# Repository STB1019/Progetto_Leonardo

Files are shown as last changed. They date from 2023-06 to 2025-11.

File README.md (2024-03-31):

<br/>
<p align="center">
  <h1 align="center">Progetto Leonardo</h1>

  <p align="center">
    An IEEE Student Branch Project
    <br/>
    <br/>
  </p>
</p>

<!--![Downloads](https://img.shields.io/github/downloads/STB1019/Progetto_Leonardo/total) ![Contributors](https://img.shields.io/github/contributors/STB1019/Progetto_Leonardo?color=dark-green)  ![Issues](https://img.shields.io/github/issues/STB1019/Progetto_Leonardo) ![Stargazers](https://img.shields.io/github/stars/STB1019/Progetto_Leonardo?style=social)
-->
## Table Of Contents

* [About the Project](#about-the-project)
* [Built With](#built-with)
* [Roadmap](#roadmap)
* [Authors](#authors)

## About The Project

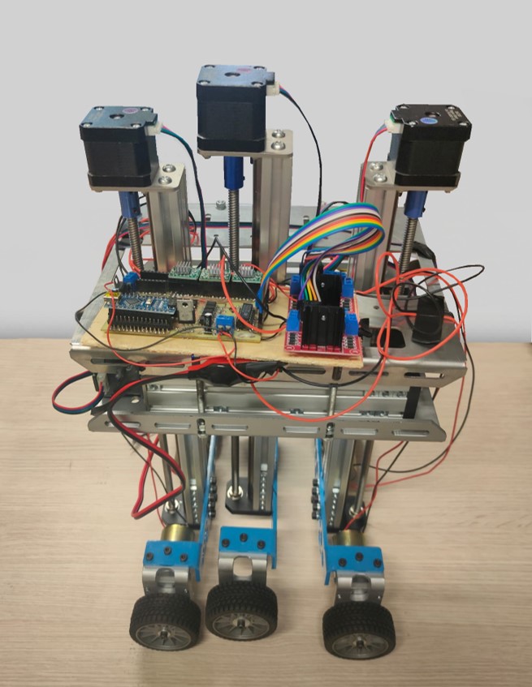
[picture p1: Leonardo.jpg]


Project with the aim of building a robot that is able to move and climb stairs.

## Built With

Raspberry and Arduino

## Roadmap

See the [open issues](https://github.com/TTT357C/Progetto_Leonardo/issues) for a list of proposed features (and known issues). </br>
See also our trello [Trello](https://trello.com/b/dbFiTYEp/progetto-leonardo-ieee-student-branch-brescia)

## Authors

* **Thomas Causetti** - *Engineering Student and Member of IEEE* - [Thomas Causetti](https://github.com/TTT357C/) - *Programmer and Designer*
* **Mirko Rossi** - *Engineering Student and Member of IEEE* - [Mirko Rossi](https://github.com/Zphyr19) - *Programmer*
* **Abdel** - *Engineering Student and Member of IEEE* - [Abdel](https://github.com/99Abdel) - *Programmer*
* **Stefano Molari** - *Engineering Student and Member of IEEE* - [Stefano Molari](https://github.com/steMola) - *Circuit Designer*

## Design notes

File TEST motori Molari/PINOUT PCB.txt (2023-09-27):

STEPPER 1
	7 - DIR
	8 - STEP 

STEPPER 2 
	9 - DIR
	10 - STEP 

STEPPER 3
	11 - DIR
	12 - STEP 

STEPPER 4
	13 - DIR
	AO - STEP 

CONNETTORE LATERALE SINISTRO
 ( DA ALTO VERSO BASSO )

5
!5 
4
!4
3
!3
2
!2

6 PWM

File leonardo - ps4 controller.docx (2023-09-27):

Modulo USB:

https://maker.pro/arduino/projects/how-to-control-an-arduino-robot-with-a-ps4-bluetooth-controller

LoRa:

https://docs.arduino.cc/learn/communication/lorawan-101

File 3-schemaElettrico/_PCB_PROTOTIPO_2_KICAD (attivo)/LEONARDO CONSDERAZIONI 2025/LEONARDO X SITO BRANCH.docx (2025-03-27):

LEONARDO 2.0

COSA È

Leonardo è la prosecuzione di un progetto storico, è essenzialmente un veicolo a batteria in grado di muoversi in ambiente urbano, riuscendo a salire anche le scale.

È stato sviluppato un primo prototipo, il cui miglioramento è stato ostacolato dal poco tempo a disposizione dei vari membri

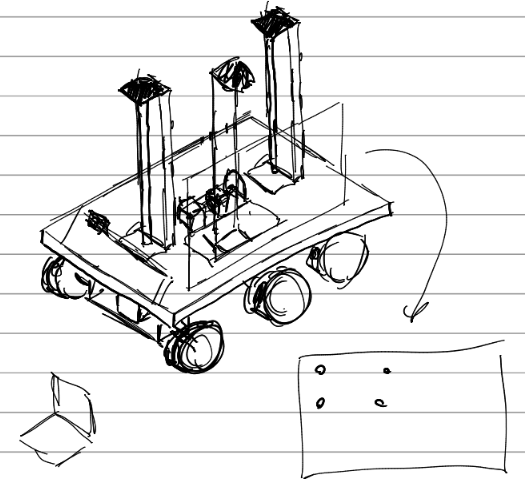
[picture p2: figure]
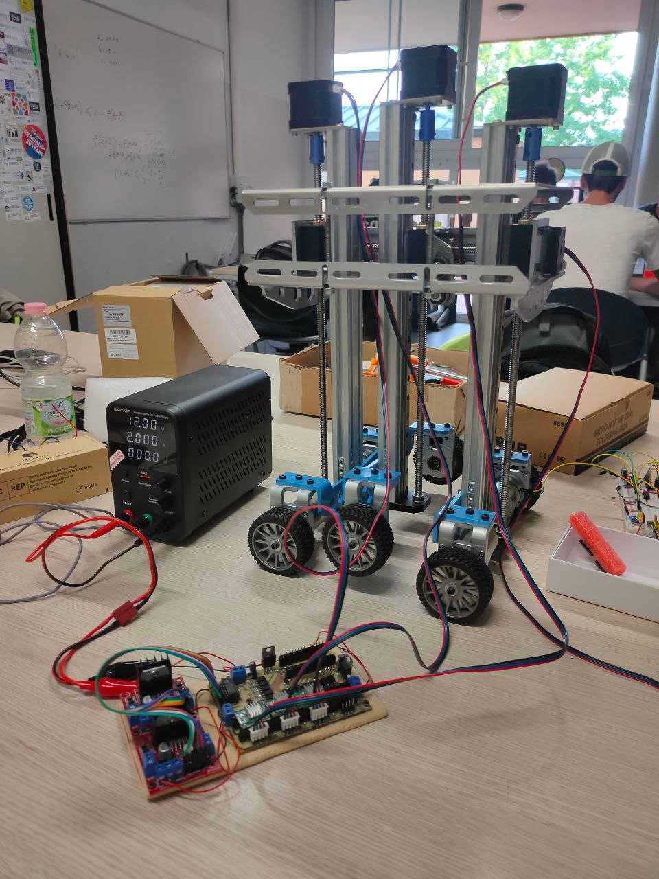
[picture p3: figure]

COSA HA A BORDO

- 4 motori DC muniti di ruota gommata per il movimento orizzontale
- 3 motori stepper che pilotano 3 assi lineari per il movimento vertivale
- 1 motore stepper per spostare l’asse centrale orizzontalmente
- Una scheda elettronica di comando dei motori
- Una rasperry PI

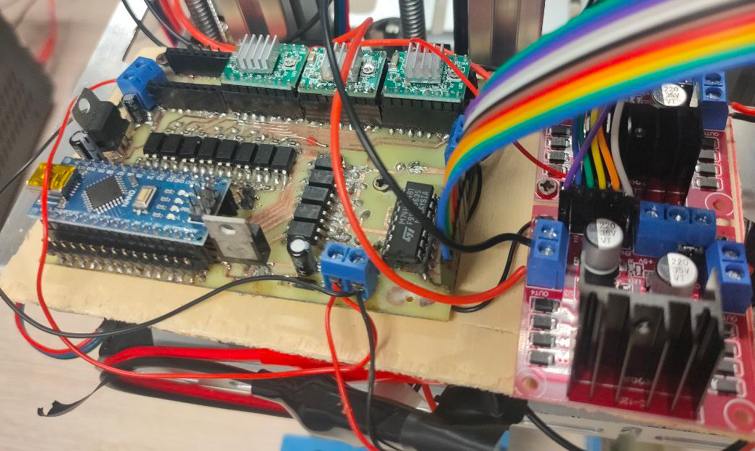
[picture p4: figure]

PROBLEMI ATTUALI

L’elettronica è da rifare, visto che si tratta di una versione base, non ottimizzata, che aveva il solo scopo di dimostrare una effettiva realizzabilità dell’idea. Bisogna migliorare gli aspetti di power saving, visto che è un sistema a batteria. Il firmware e il software sono da integrare con la nuova elettronica.

LAVORI IN CORSO

Si è pensato di adottare un’architettura modulare in modo da poter garantire flessibilità verso sviluppi futuri. È in programma lo sviluppo di:

- Una board per distribuire efficacemente la potenza a tutte le schede del sistema, si ipotizza di tipologia switching per garantire un’efficienza sopra al 90%
- Una board che si interfaccia ai servomotori e ai motori DC, occupandosi quindi di pilotare i movimenti del mezzo
- Una board che si occupa di acquisire posizione ei segnali dall’ambiente circostante, fornendo le informazioni necessarie alla navigazione del mezzo.
- Un raspberry PI che faccia da mente, occupandosi di acquisire i segnali dalla board sensori e di produrre gli output necessari alla board motori

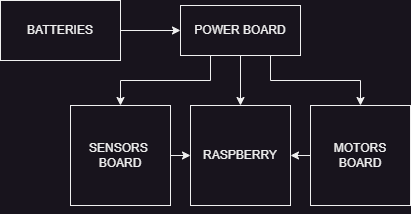
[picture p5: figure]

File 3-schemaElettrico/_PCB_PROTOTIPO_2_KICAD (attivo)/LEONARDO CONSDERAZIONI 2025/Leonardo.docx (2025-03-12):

Partendo dal presupposto che si vuole riciclare la meccanica precedente

STEPPER MOTOR DRIVER

https://lastminuteengineers.com/a4988-stepper-motor-driver-arduino-tutorial/

Dal datasheet a4988

Per maggiore flessibilità è stato lasciata al firmware la scelta del microstep resolution del motore.

I 4 driver saranno collegati tra di loro.

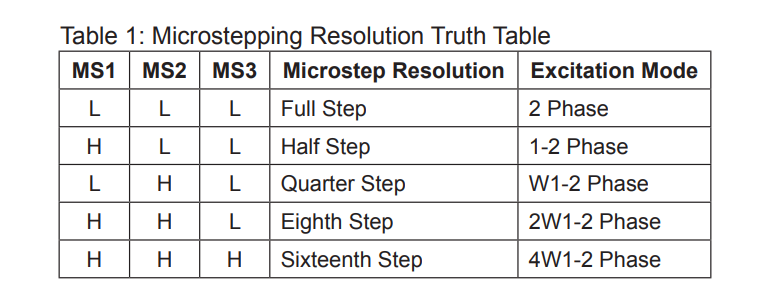
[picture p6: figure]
Immagine che contiene testo, Carattere, schermata, numero Il contenuto generato dall'IA potrebbe non essere corretto.

BATTERY LEVEL

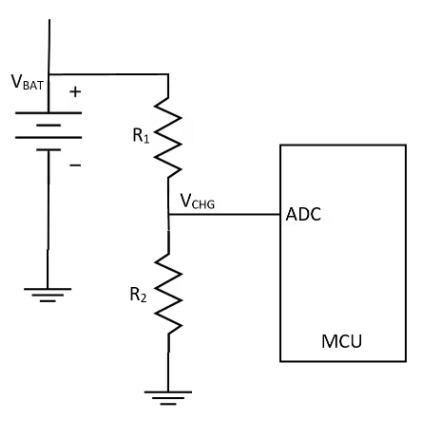
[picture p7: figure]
Immagine che contiene diagramma, schizzo, Disegno tecnico, Piano Il contenuto generato dall'IA potrebbe non essere corretto.

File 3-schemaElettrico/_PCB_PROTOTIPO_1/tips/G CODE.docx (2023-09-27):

G CODE

; Ender 3 Custom Start G-code

G92 E0 ; Reset Extruder

G28 ; Home all axes

G1 Z2.0 F3000 ; Move Z Axis up little to prevent scratching of Heat Bed

G1 X0.1 Y20 Z0.3 F5000.0 ; Move to start position

G1 X0.1 Y200.0 Z0.3 F1500.0 E15 ; Draw the first line

G1 X0.4 Y200.0 Z0.3 F5000.0 ; Move to side a little

G1 X0.4 Y20 Z0.3 F1500.0 E30 ; Draw the second line

G92 E0 ; Reset Extruder

G1 Z2.0 F3000 ; Move Z Axis up little to prevent scratching of Heat Bed

G1 X5 Y20 Z0.3 F5000.0 ; Move over to prevent blob squish

G0 si muove senza estrudere

G1 si muove con l’estrusore

G90 set posizione assoluta

G91 set posizione relativa

G28 auto home

M104

M109

M140

M190

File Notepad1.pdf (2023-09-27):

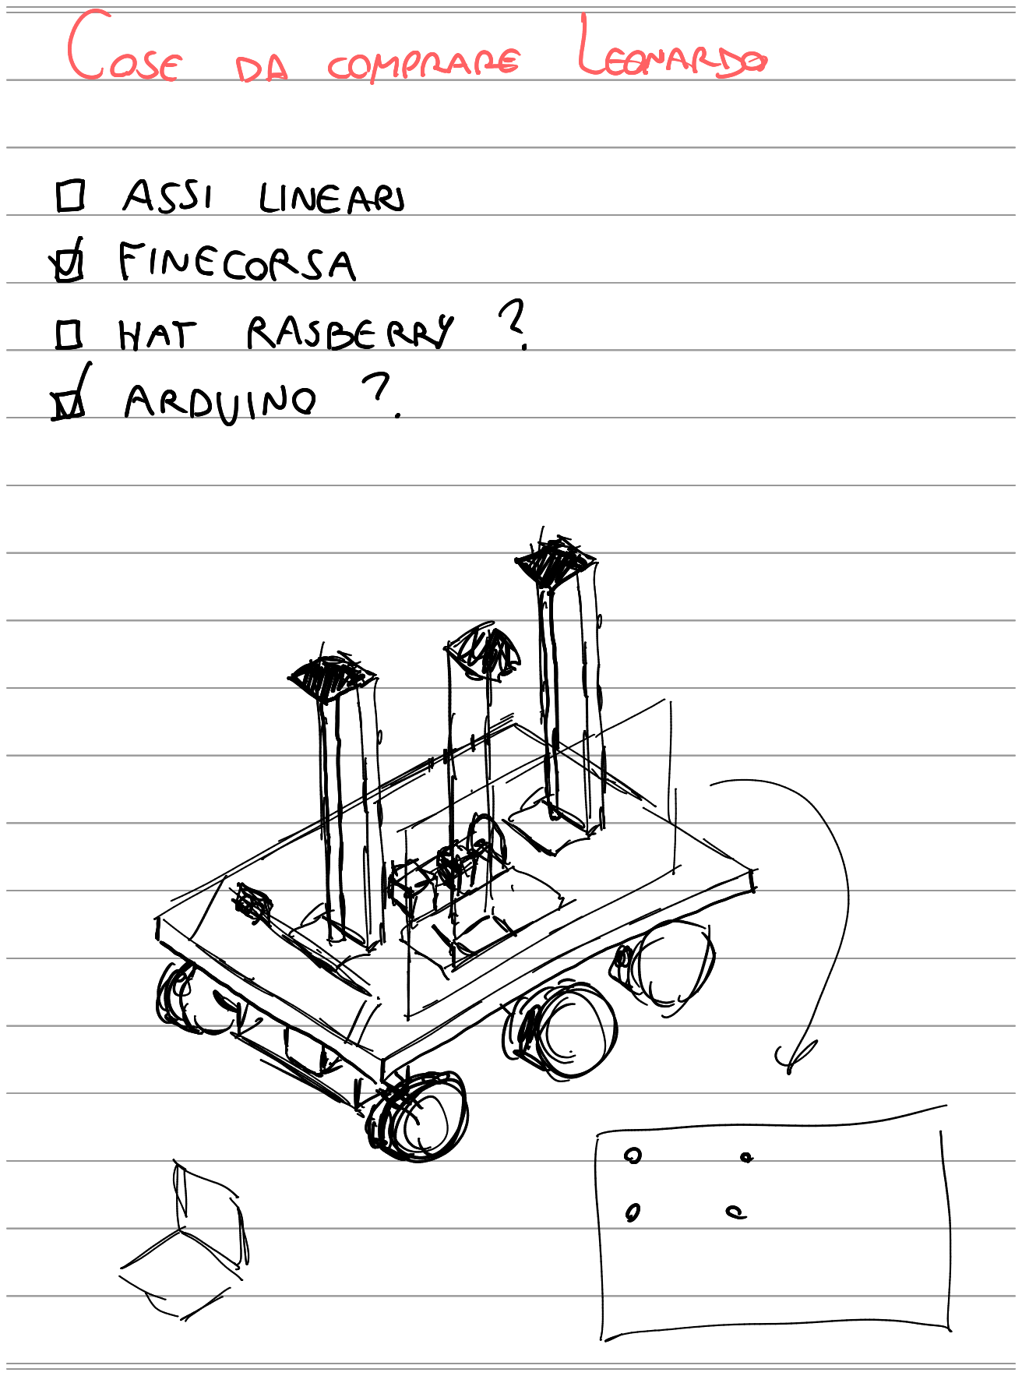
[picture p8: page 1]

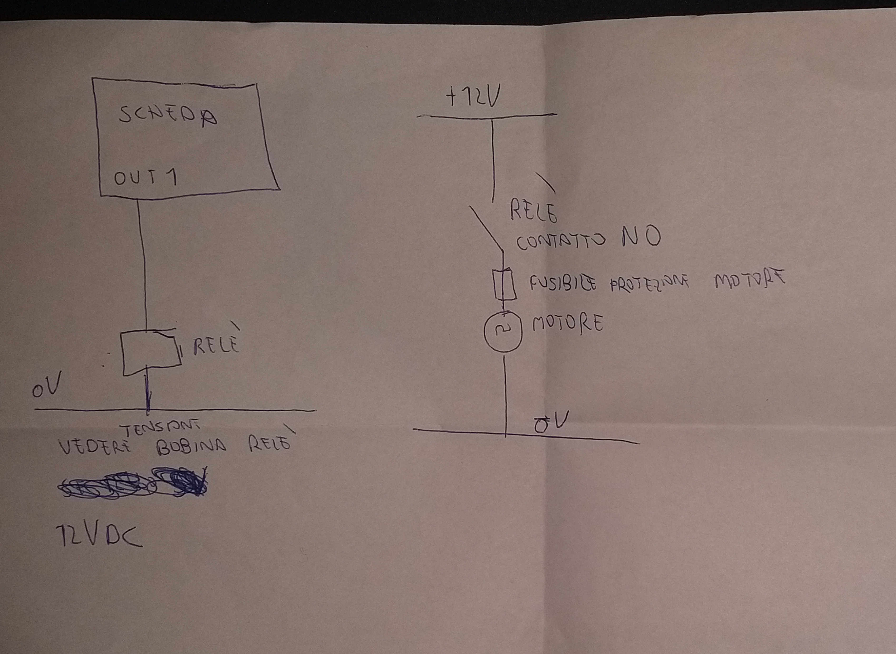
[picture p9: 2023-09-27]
PROTO_SCHEMA_MOTORI.jpg

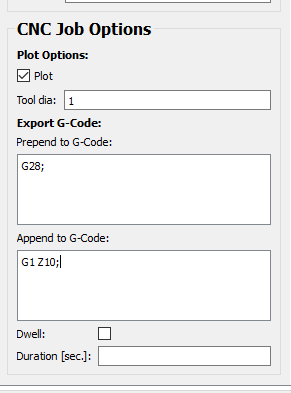
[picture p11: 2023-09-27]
3-schemaElettrico/_PCB_PROTOTIPO_1/02 FLATCAM/CNC OPTIONS.PNG

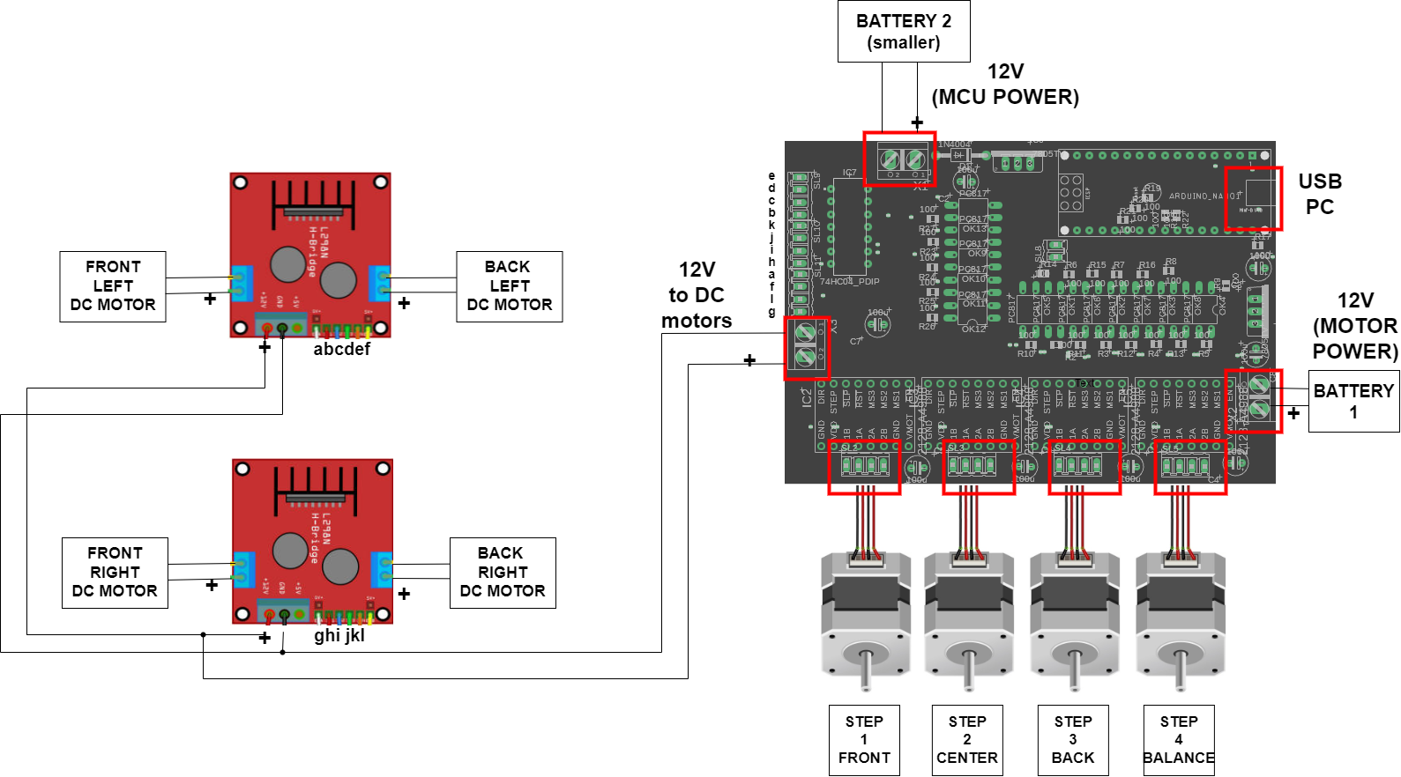
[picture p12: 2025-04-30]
3-schemaElettrico/_PCB_PROTOTIPO_1/PCB Leonardo.drawio.png

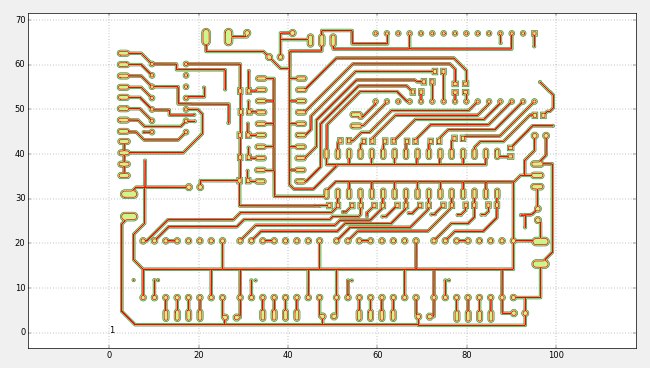
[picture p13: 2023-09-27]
3-schemaElettrico/_PCB_PROTOTIPO_1/02 FLATCAM/foto copper top iso.PNG

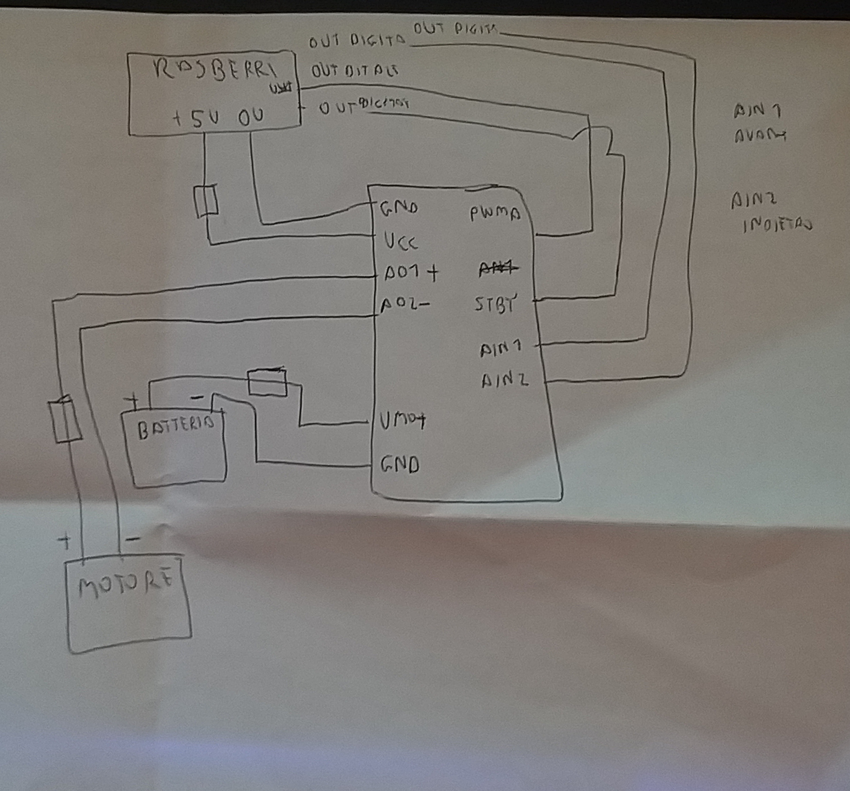
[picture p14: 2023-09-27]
4-Datasheet/vario scartato/MOTORI_LEONARDO_2.jpg

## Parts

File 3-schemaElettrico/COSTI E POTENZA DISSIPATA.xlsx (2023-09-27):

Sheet: COSTO
NOME | COSTO UNITARIO | QUANTITA' | COSTO PARZIALE
ASSE LINEARE
DRIVER A4966 |  | 4
DRIVER TB6612FNG |  | 2
ARDUINO NANO |  | 1
BATTERIE
OPTO ISOLATORI

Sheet: CONSUMI
POTENZA DISPONIBILE |  |  |  | consumo fisso
 |  |  |  | (indipendente dalla fase in cui mi trovo)
POTENZA DISSIPATA TOTALE
 | TEMPO DI FUNZIONAMENTO MASSIMO DEL SISTEMA
 | CONSUMO PER SALIRE LE SCALE
 | componenti attivi | qtà | P singolo
 | stepper | 4
 | dc | 4
 | optoisolatori | 12
 | comsumo fisso
 | CONSUMO PER GIRARE SOLO CON I DC
 | componenti attivi | qtà | P singolo
 | dc | 4
 | optoisolatori | 4
 | comsumo fisso
 | CONSUMO RASPBERRY
 | CONSUMO ARDUINO

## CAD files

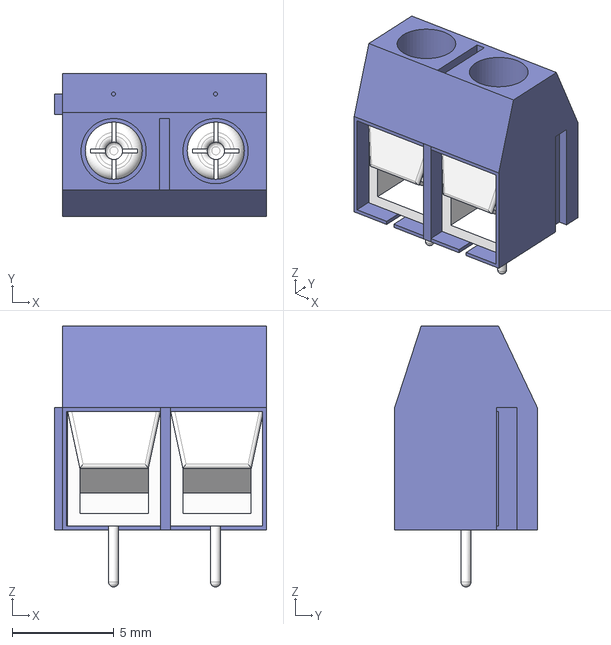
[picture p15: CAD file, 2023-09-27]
3-schemaElettrico/3D MODELS/ak500 - 2.step
10.4 x 7.00 x 12.8 mm

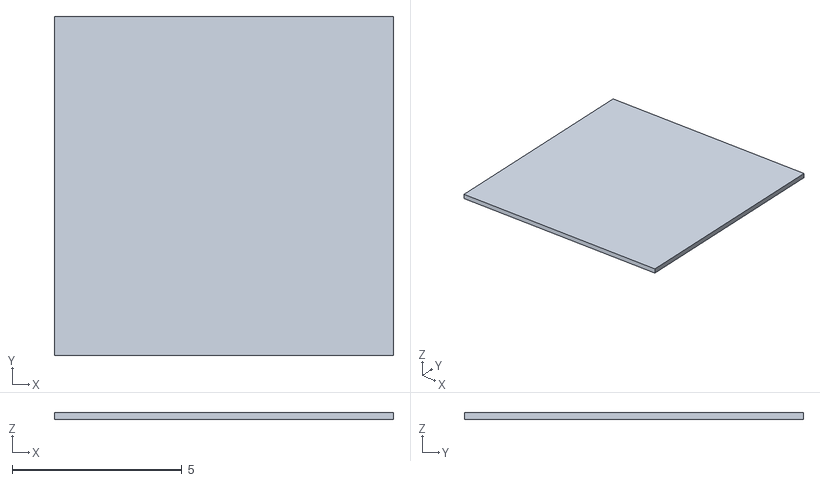
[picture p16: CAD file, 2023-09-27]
3-schemaElettrico/_PCB_PROTOTIPO_1/tips/ORIGINE.stl
10.0 x 10.0 x 0.2

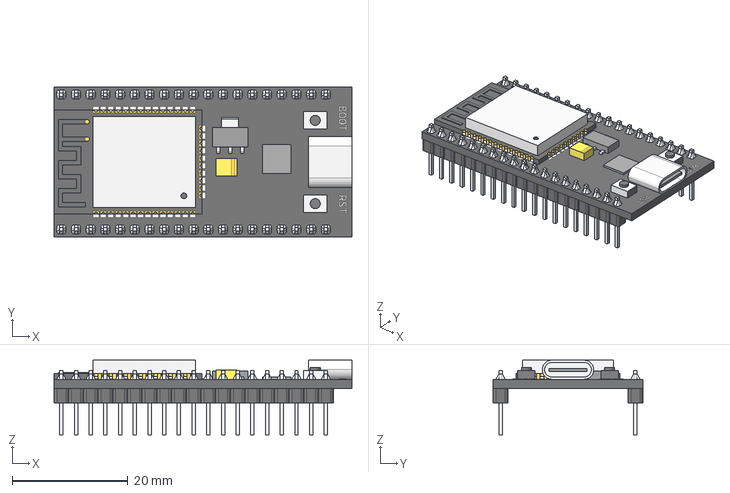
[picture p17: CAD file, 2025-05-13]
3-schemaElettrico/_PCB_PROTOTIPO_2_KICAD (attivo)/LIBRERIE ESTERNE/NodeMCU-32S-USBC-38pin-Narrow.stp
51.5 x 25.9 x 12.9 mm

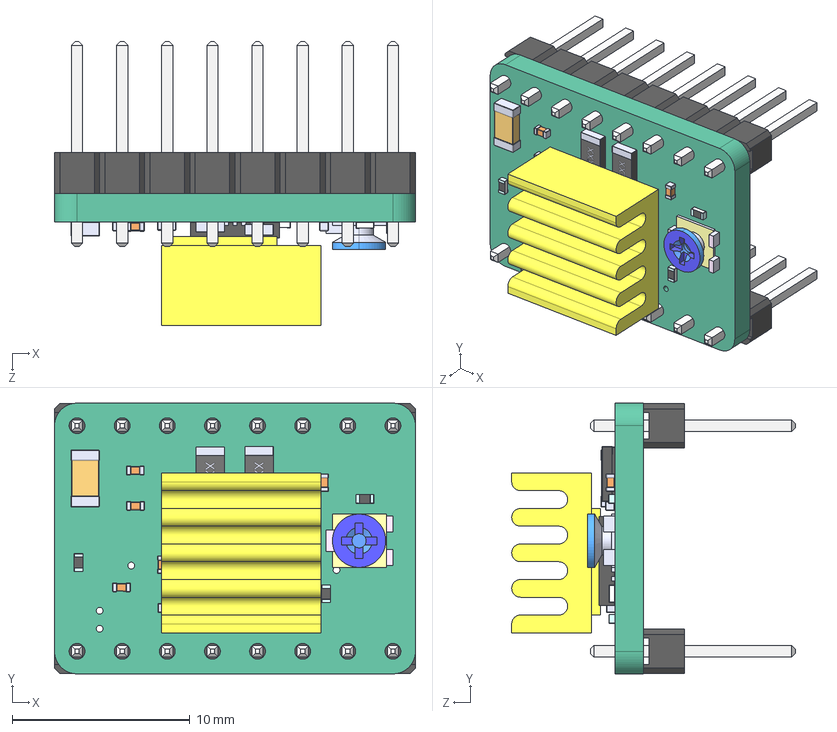
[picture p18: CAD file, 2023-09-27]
3-schemaElettrico/3D MODELS/A4988-1.STEP
20.3 x 15.2 x 16.0 mm
stepstick
QFN28ET_A4983
TRIMPOT3MM_TRIMPOTSMD
Pin header pitch 2.54mm_08 contacts x 2
Heatsink For A4988
R0402-01 x 4
R1206-01 x 2
C0402 x 6
C1206B

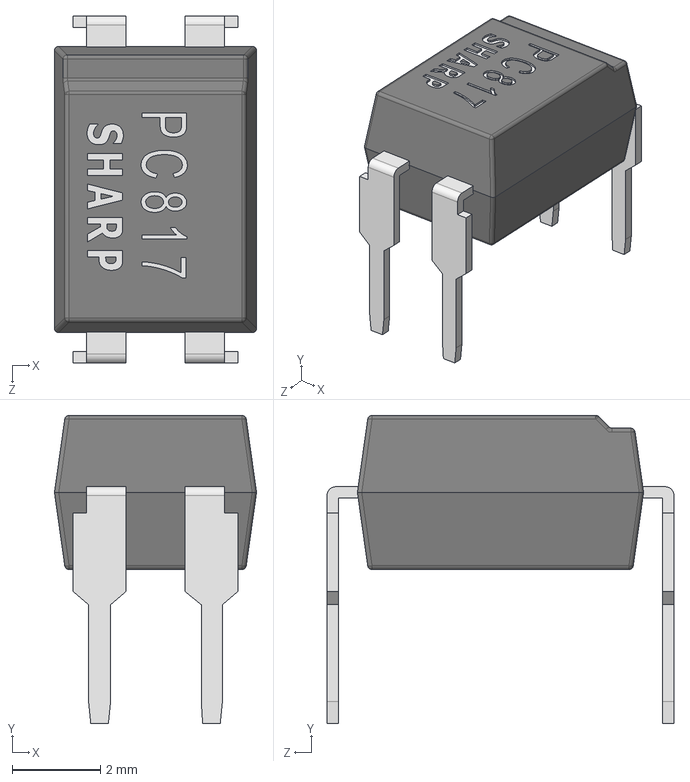
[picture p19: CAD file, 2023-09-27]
3-schemaElettrico/3D MODELS/pc817 dip6.step
4.59 x 7.00 x 7.88 mm

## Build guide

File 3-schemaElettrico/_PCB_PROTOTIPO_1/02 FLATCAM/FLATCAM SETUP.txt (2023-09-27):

open "gerber bottom"
	tool dia -0.6
	offset y70
	offset x69 y82
	generate 
iso
	travel z 4
	generate 
cnc
	tool dia 1
	prepend: G28; per autohome all'inizio
	append: G1 Z10; per alzare la punta alla fine
	generate gerber

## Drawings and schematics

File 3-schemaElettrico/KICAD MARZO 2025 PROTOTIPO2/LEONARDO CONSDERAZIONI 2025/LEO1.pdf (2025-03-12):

REVISION | DESCRIPTION | DATE | APPROVED | REV. SHT. <SCH DWG NO> 1 DWG. NO.

## BATTERY

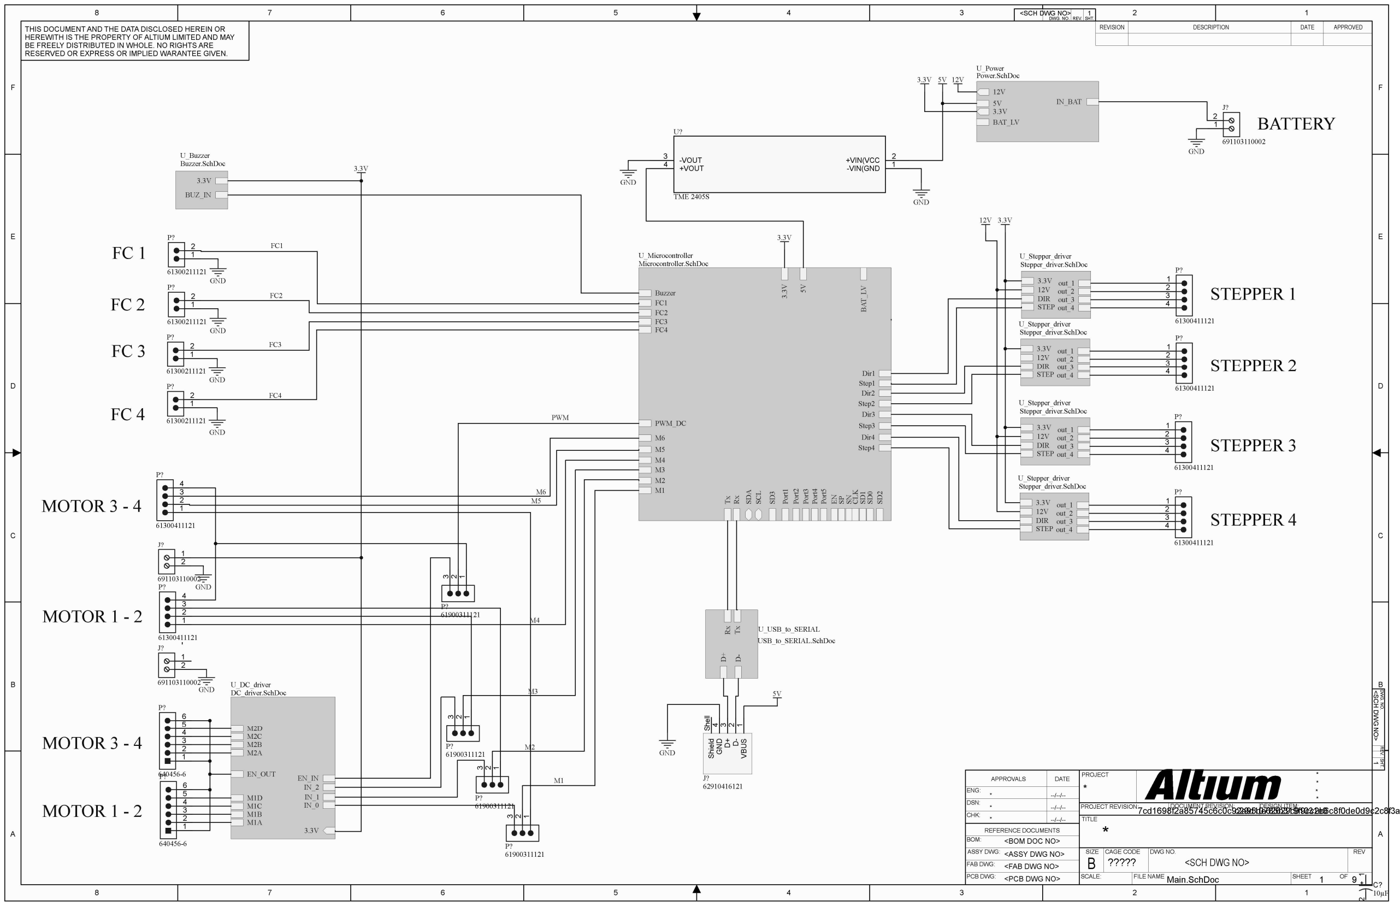
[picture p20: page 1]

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
DWG. NO. REV. SHT.

<SCH DWG NO> 1

THIS DOCUMENT AND THE DATA DISCLOSED HEREIN OR HEREWITH IS THE PROPERTY OF ALTIUM LIMITED AND MAY BE FREELY DISTRIBUTED IN WHOLE. NO RIGHTS ARE RESERVED OR EXPRESS OR IMPLIED WARANTEE GIVEN.

*

B <SCH DWG NO>

Main.SchDoc | 1 | 9

TITLE

SIZE | DWG NO.
FILE NAME | SHEET | OF

REV

SCALE:

?????

CAGE CODE

PROJECT
* | *
| *

*
*
APPROVALS | DATE

ENG:

DSN:

*

*

--/--/--

--/--/--
CHK:
--/--/--
REFERENCE DOCUMENTS
BOM:

ASSY DWG:

FAB DWG:
PCB DWG: <PCB DWG NO>

<FAB DWG NO>

<ASSY DWG NO>

<BOM DOC NO>

*

PROJECT REVISION: | DOCUMENT REVISION: | DESIGN ITEM: 7cd1698f2a85745c6c0c92a95de62629c91031e0 c29d10785b319f9cc2b6c8f0de0d9c2c8f3a0468 1 2

10µF

C?

BUZ_IN

3.3V

U_Buzzer
Buzzer.SchDoc

GND

2
1

P?

61300211121

GND

2
1

P?

61300211121

GND

2
1

P?

61300211121

GND

2
1

P?

61300211121

2

1

3
4

P?

61300411121

STEP

DIR

3.3V
12V

out_1
out_2
out_3
out_4

U_Stepper_driver
Stepper_driver.SchDoc

2

1

3
4

P?

61300411121

STEP

DIR

3.3V
12V

out_1
out_2
out_3
out_4

U_Stepper_driver
Stepper_driver.SchDoc

2

1

3
4

P?

61300411121

STEP

DIR

3.3V
12V

out_1
out_2
out_3
out_4

U_Stepper_driver
Stepper_driver.SchDoc

2

1

3
4

P?

61300411121

STEP

DIR

3.3V
12V

out_1
out_2
out_3
out_4

U_Stepper_driver
Stepper_driver.SchDoc

3.3V

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
IN_0

IN_1

IN_2

EN_IN EN_OUT

U_DC_driver
DC_driver.SchDoc

1

2

3

4

5

6

P?

640456-6

1

2

3

4

5

6

P?

640456-6

## MOTOR 3 - 4

## MOTOR 1 - 2

## STEPPER 1

## STEPPER 2

## STEPPER 3

## STEPPER 4

FC 1

FC 2

FC 3

FC 4

1
2

J?

691103110002

1
2

J?

691103110002

Dir1
Step1
Dir2
Step2
Dir3
Step3
Dir4

Step4 ³.3V TxRx SDA SCL SD³ Port1 Port2 Port3 Port4 Port5 ENSPSNCLK SD¹ SD⁰ SD² ⁵V

M2

M3

M4

M5

M6

Buzzer

FC3

FC1

FC4

FC2

M1

PWM_DC | BAT_LV

U_Microcontroller
Microcontroller.SchDoc

## MOTOR 1 - 2

## MOTOR 3 - 4

3

2

1

P?

61900311121 ³

2

1

P?

61900311121 ³

2

1

P?
61900311121

3

2

1

P?
61900311121 2
1

3

4

P?

61300411121

2
1

3

4

P?

61300411121

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
3.3V

5V

BAT_LV

IN_BAT

U_Power
Power.SchDoc

1

2

J?

691103110002
GND

GND

GND | D⁺ | D⁻ RxTx | U_USB_to_SERIAL
USB_to_SERIAL.SchDoc VBUS

### 1 D- 2 D+

### 3 GND

## 4 Shield Shell

J?
62910416121

GND

3.3V 5V 12V

12V 3.3V

3.3V

5V

-VIN(GND | 1
+VIN(VCC | 2

-VOUT 3
+VOUT 4

U?

TME 2405S

GND

GND

3.3V

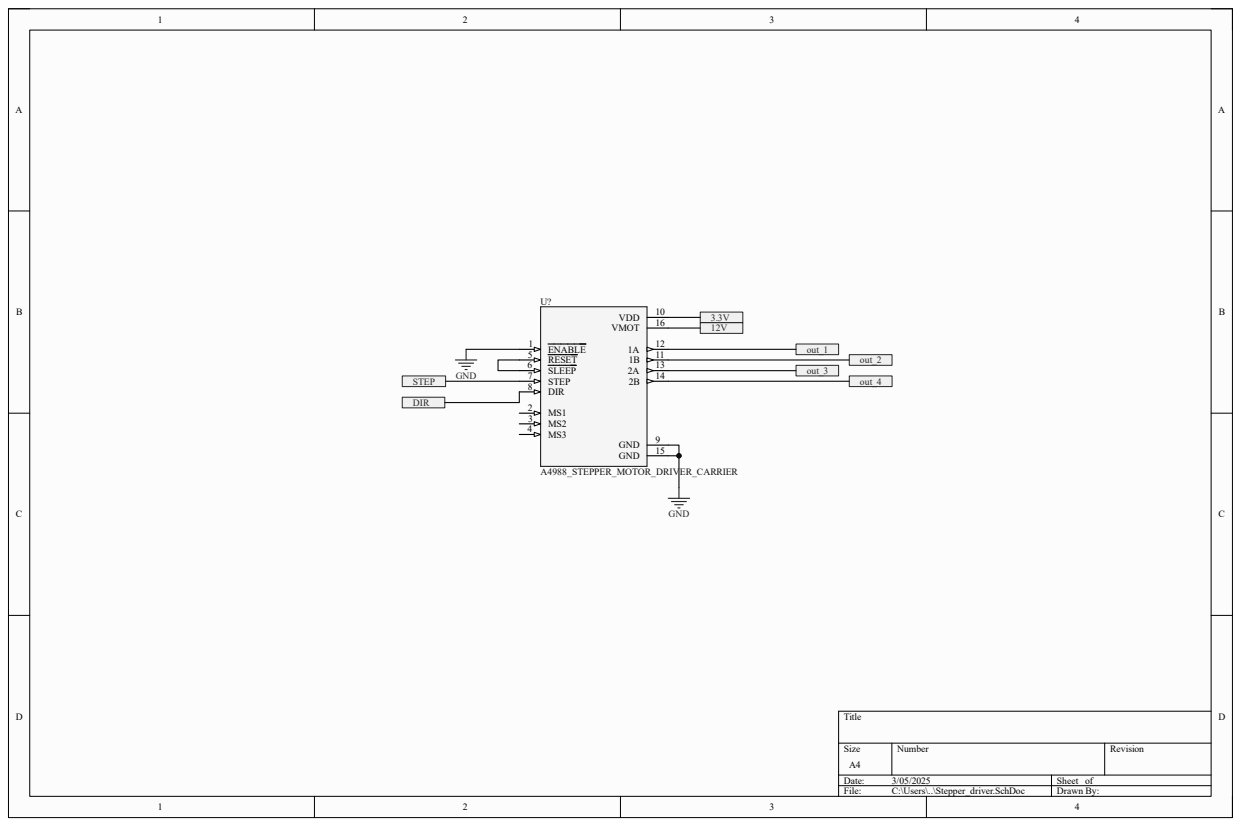
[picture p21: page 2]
Title; Size; Number; Revision; Date:; Sheet of; File:; C:\Users\..\Stepper_driver.SchDoc; Drawn By:; STEP; DIR; ENABLE 1 RESET 5 SLEEP 6 STEP 7 DIR 8; VDD; VMOT; GND; A4988_STEPPER_MOTOR_DRIVER_CARRIER; out_1; out_2; out_3; out_4

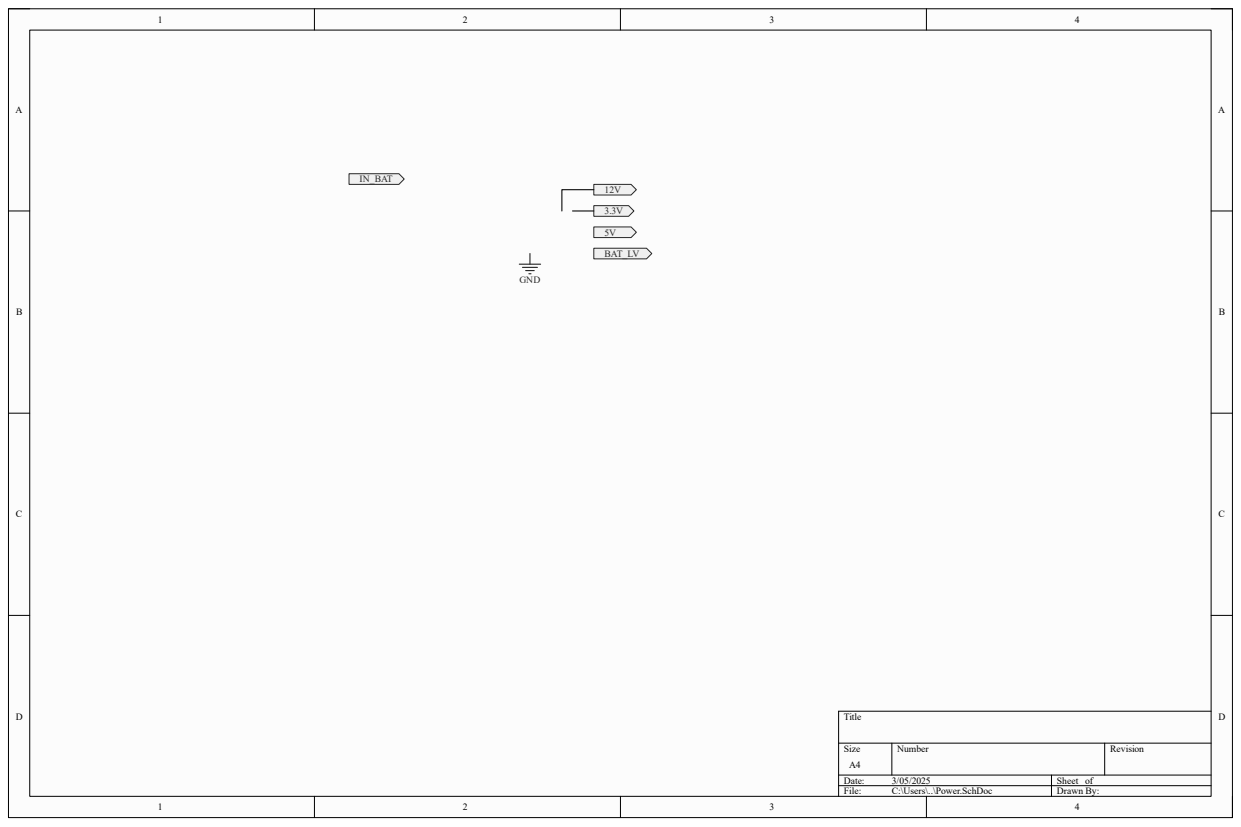
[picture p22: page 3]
Title; Size; Number; Revision; Date:; Sheet of; File:; C:\Users\..\Power.SchDoc; Drawn By:; GND; BAT_LV; IN_BAT

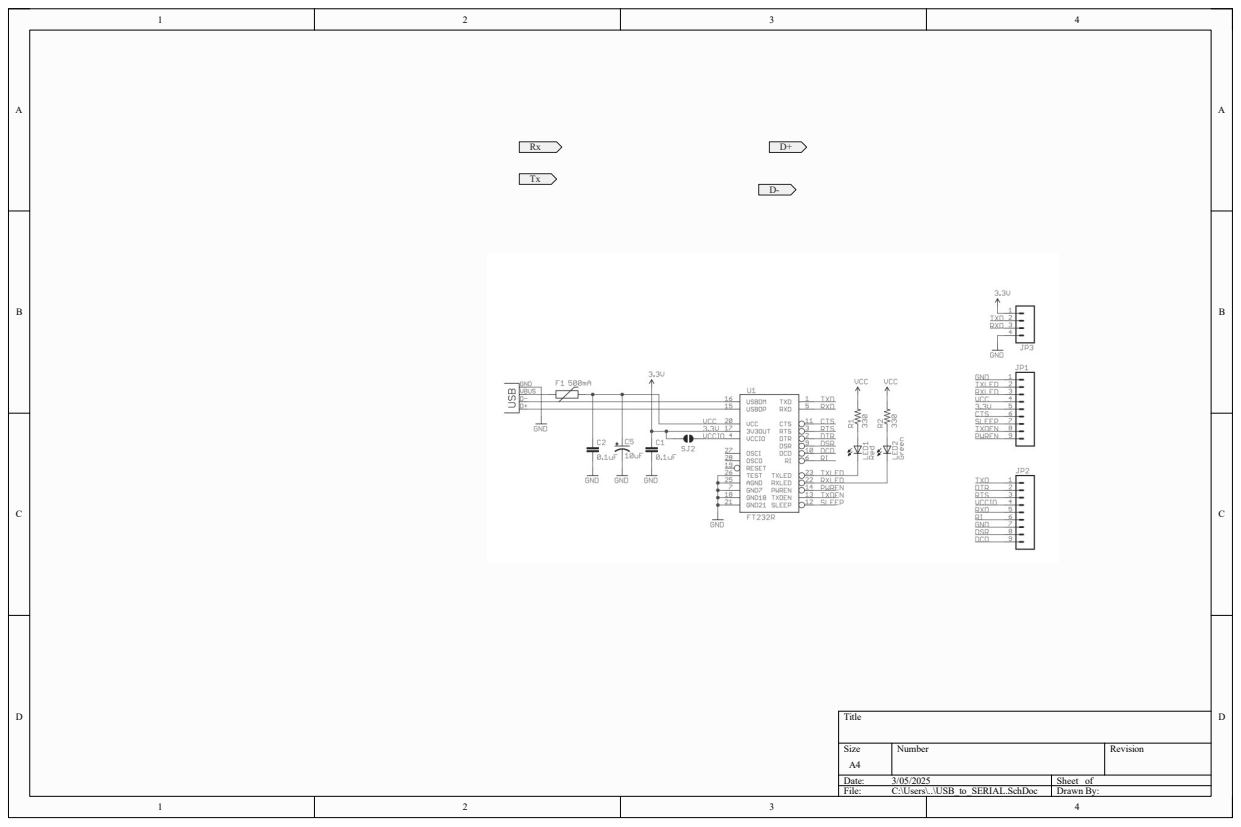
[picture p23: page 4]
Title; Size; Number; Revision; Date:; Sheet of; File:; C:\Users\..\USB_to_SERIAL.SchDoc; Drawn By:

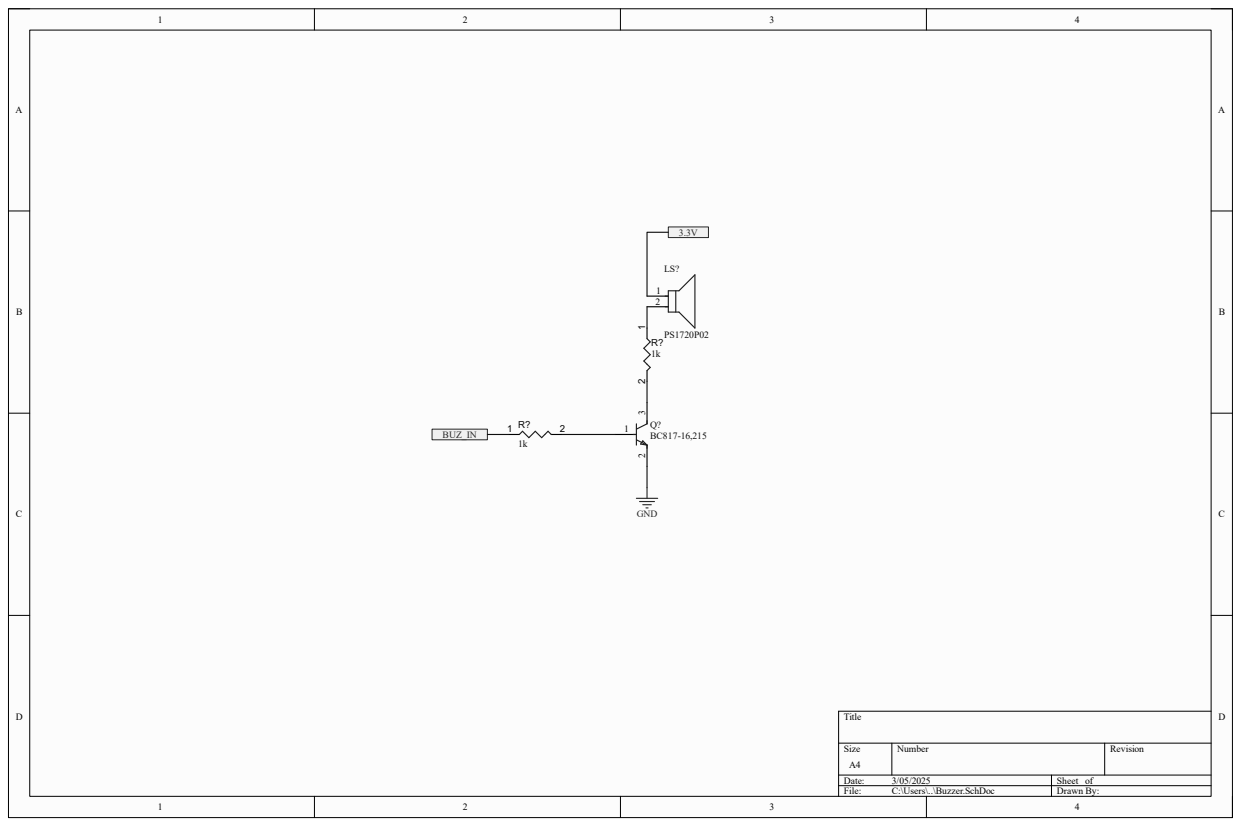
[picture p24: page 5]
Title; Size; Number; Revision; Date:; Sheet of; File:; C:\Users\..\Buzzer.SchDoc; Drawn By:; BUZ_IN; GND

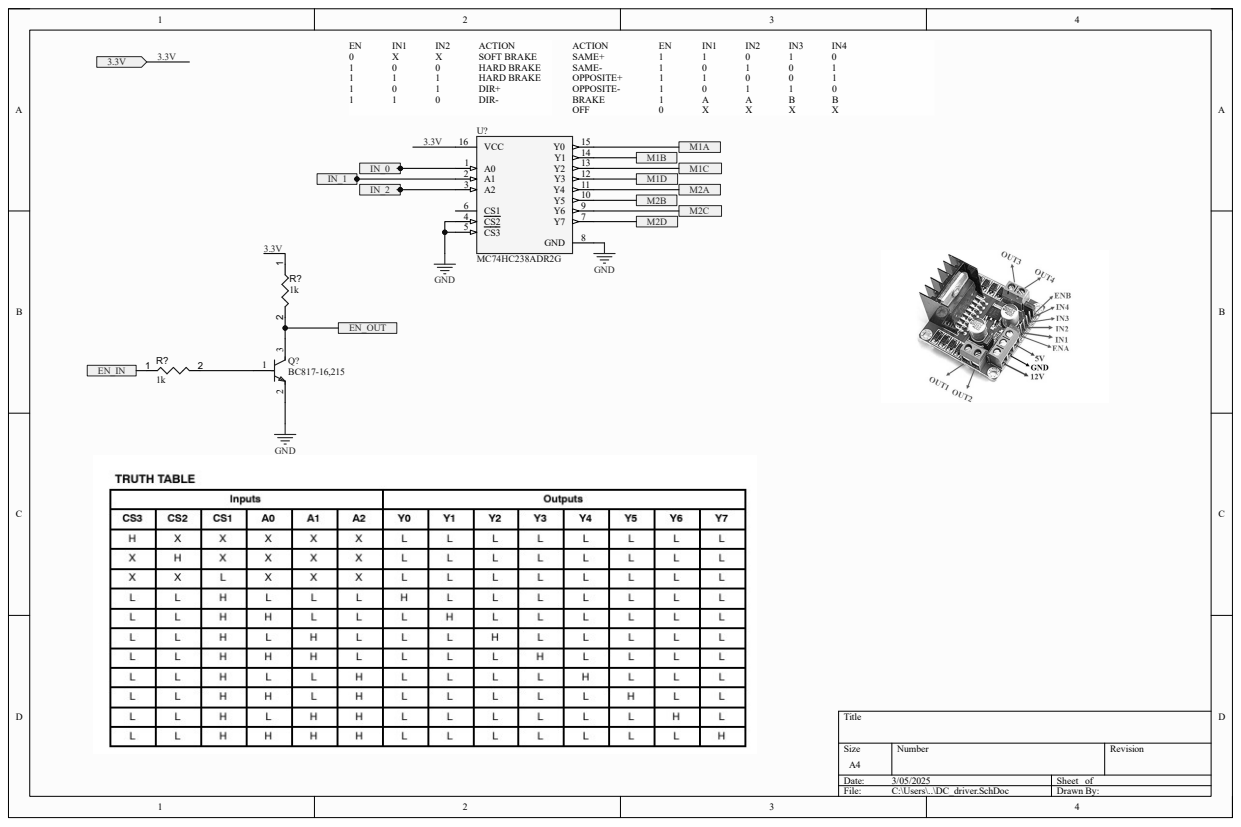
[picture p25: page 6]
Title; Size; Number; Revision; Date:; Sheet of; File:; C:\Users\..\DC_driver.SchDoc; Drawn By:; ACTION; SOFT BRAKE; HARD BRAKE; DIR+; DIR-; SAME+; SAME-; OPPOSITE+; OPPOSITE-; BRAKE; OFF; VCC 16; GND; MC74HC238ADR2G; EN_OUT

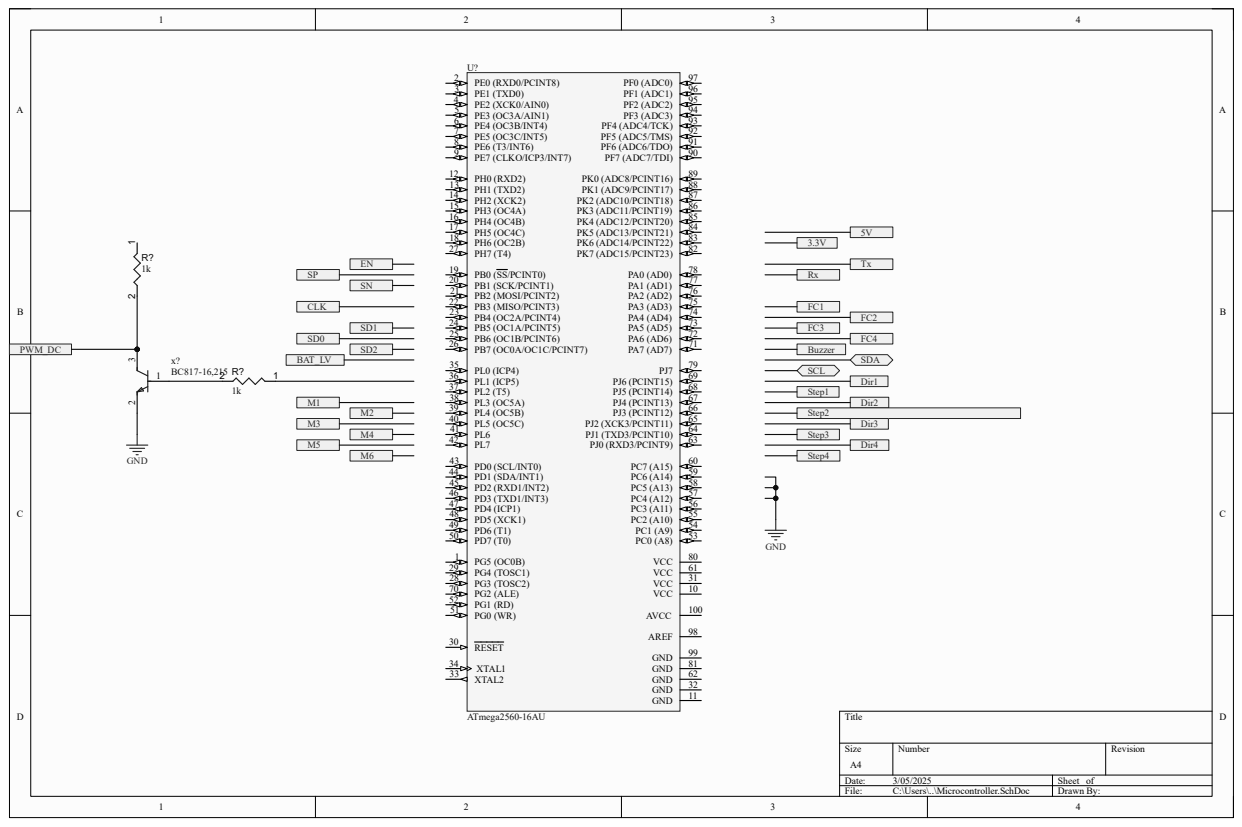
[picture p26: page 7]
Title; Size; Number; Revision; Date:; Sheet of; File:; C:\Users\..\Microcontroller.SchDoc; Drawn By:; Dir1; Step1; Dir2; Step2; Dir3; Step3; Dir4; Step4; SDA; SCL; GND; Buzzer; PWM_DC; BAT_LV; CLK; PJ0 (RXD3/PCINT9); AVCC; VCC; 11 GND; PD2 (RXD1/INT2) 45; RESET 30; XTAL1 34; PJ5 (PCINT14); 68 PJ6 (PCINT15); AREF; PD1 (SDA/INT1) 44; PB6 (OC1B/PCINT6) 25; PD3 (TXD1/INT3) 46 PD4 (ICP1) 47 PD5 (XCK1) 48 PD6 (T1) 49 PD7 (T0) 50; PF1 (ADC1); PF2 (ADC2); PF4 (ADC4/TCK); PF5 (ADC5/TMS); PF6 (ADC6/TDO)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

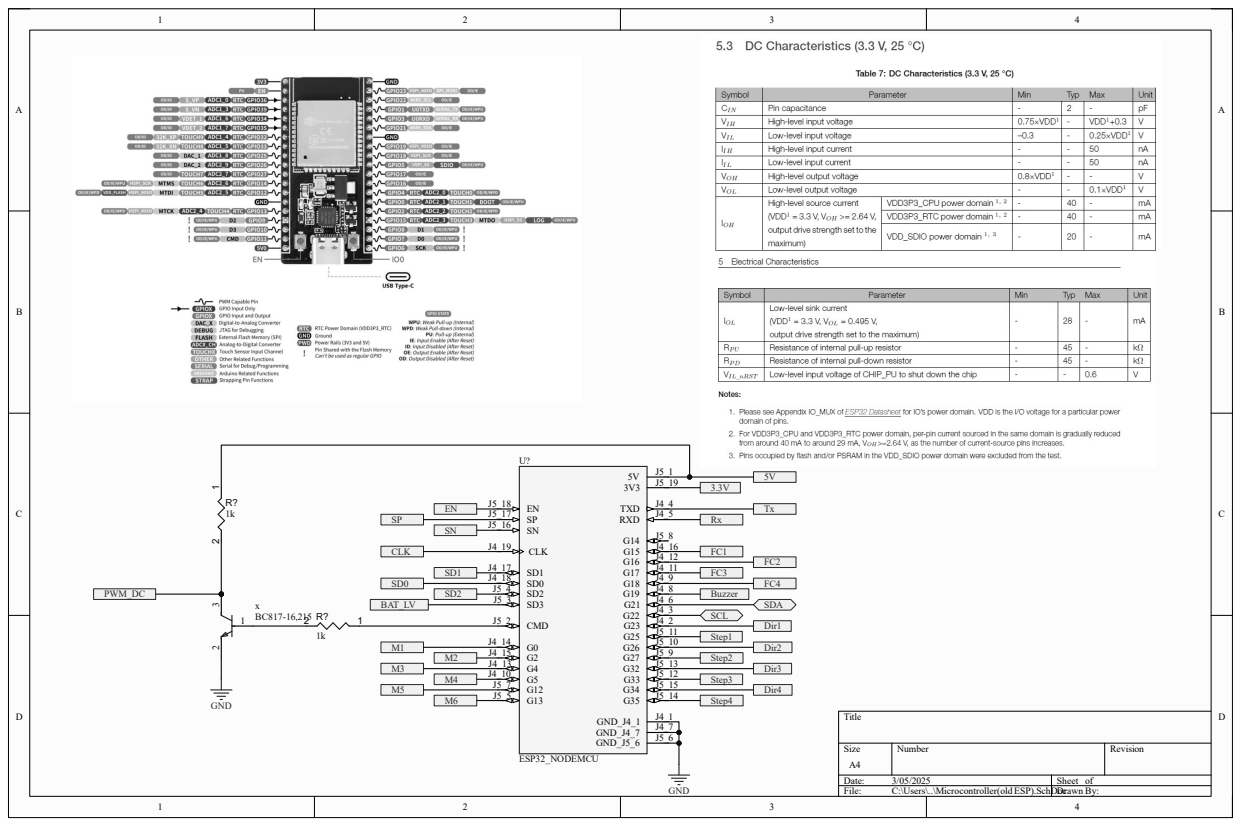
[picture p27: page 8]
Title; Size; Number; Revision; Date:; Sheet of; File:; C:\Users\..\Microcontroller(old ESP).SchDoc Drawn By:; Dir1; Step1; Dir2; Step2; Dir3; Step3; Dir4; Step4; SDA; SCL; CLK J4_19; CMD J5_2; TXD; RXD; GND_J4_1; GND_J4_7; GND_J5_6; ESP32_NODEMCU; GND; Buzzer; PWM_DC; BAT_LV; CLK

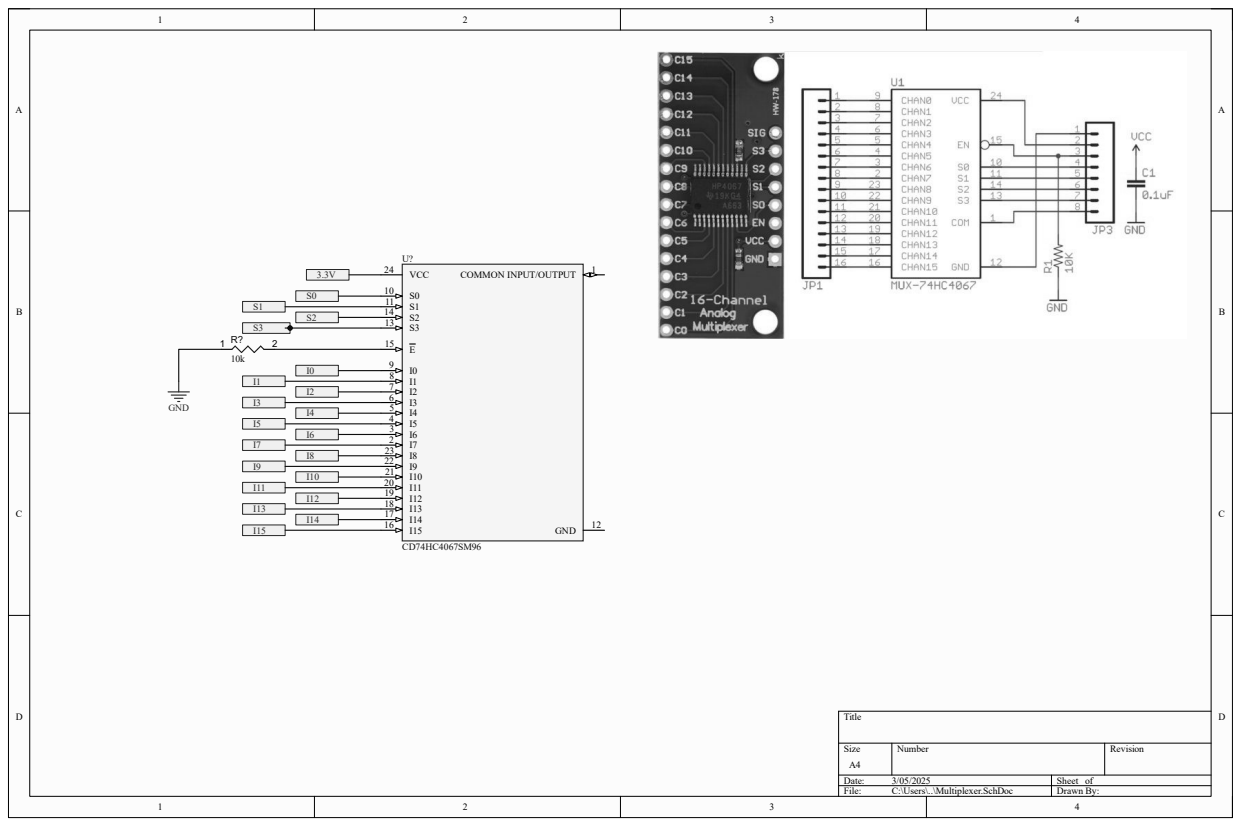
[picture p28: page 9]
Title; Size; Number; Revision; Date:; Sheet of; File:; C:\Users\..\Multiplexer.SchDoc; Drawn By:; VCC 24; COMMON INPUT/OUTPUT; GND

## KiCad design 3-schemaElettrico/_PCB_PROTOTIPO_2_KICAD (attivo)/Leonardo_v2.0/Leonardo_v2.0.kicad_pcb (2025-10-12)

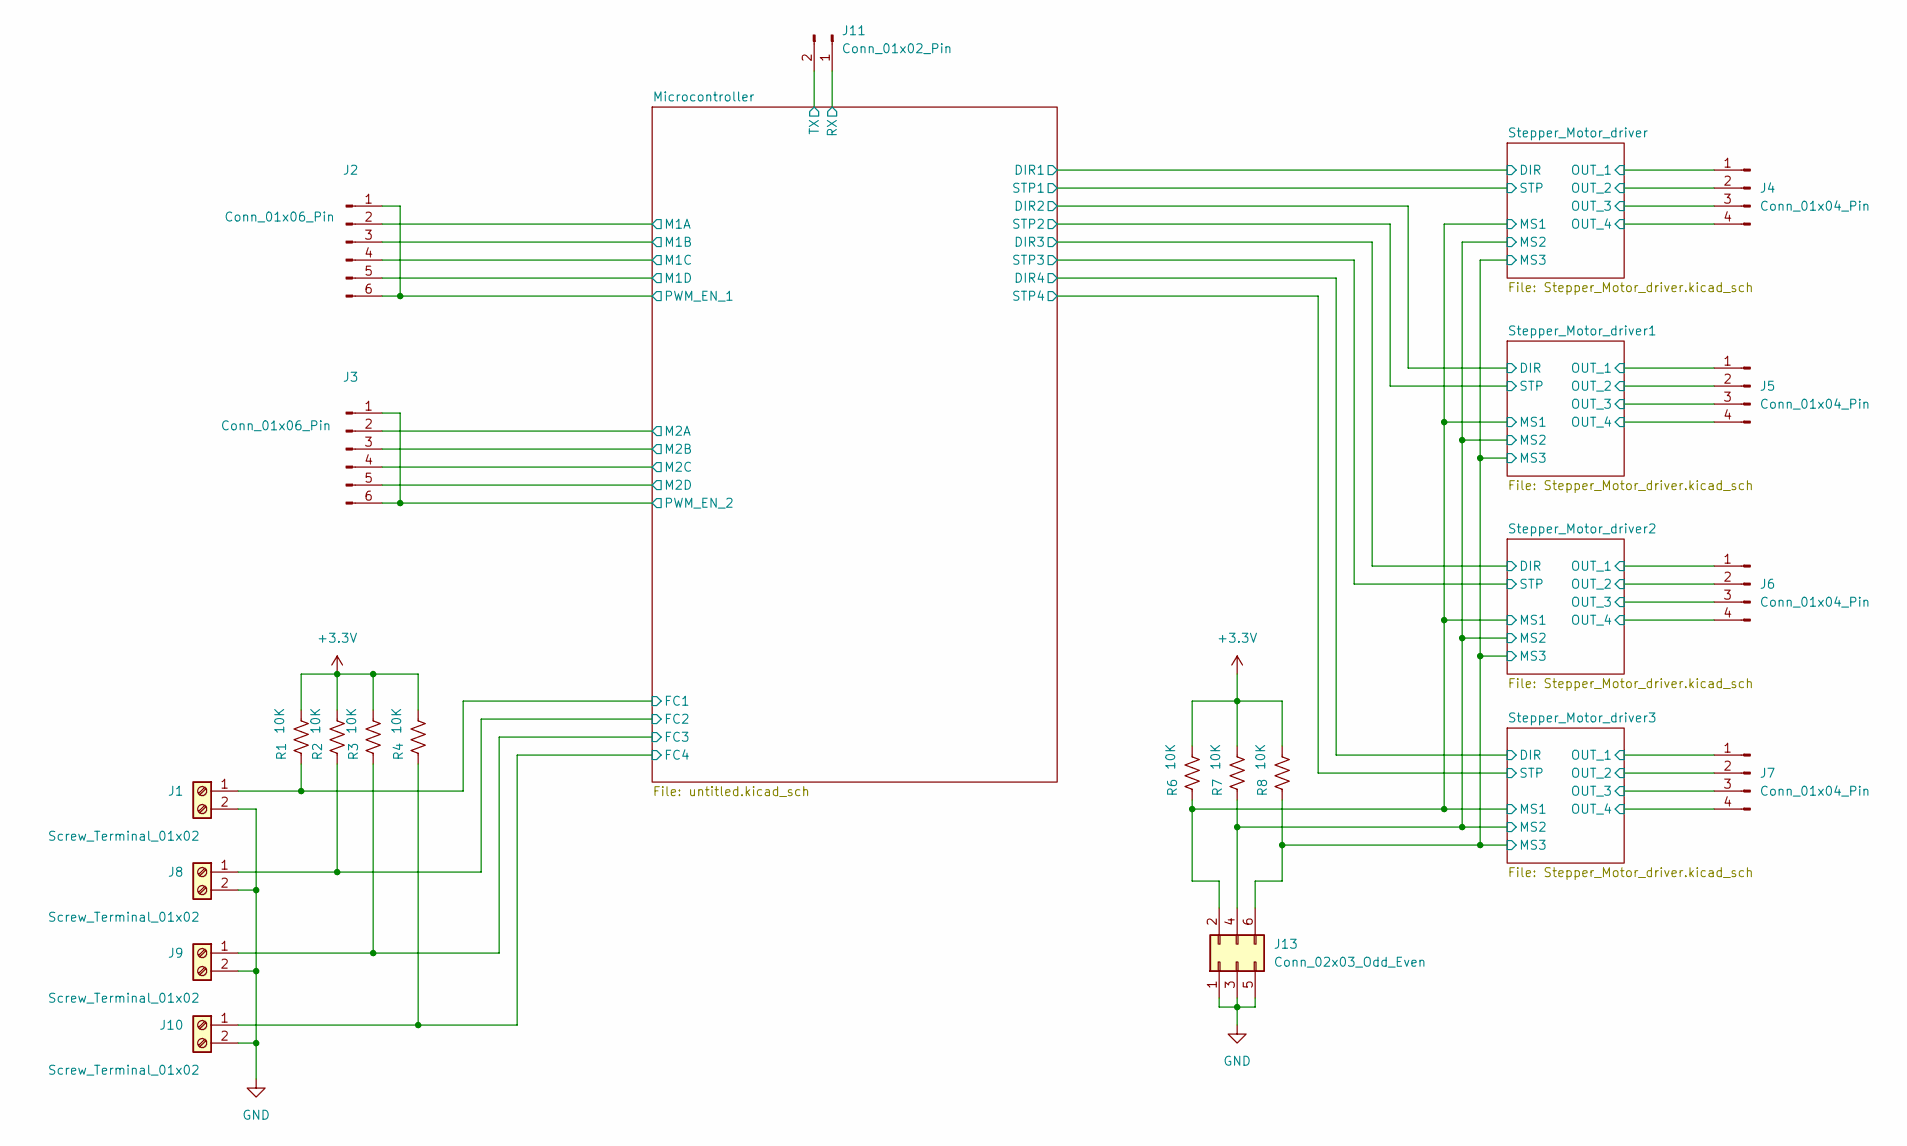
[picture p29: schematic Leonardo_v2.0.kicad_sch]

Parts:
J1, J8, J9, J10: Screw_Terminal_01x02; TerminalBlock_Phoenix_MKDS-1,5-2_1x02_P5.00mm_Horizontal
J2, J3: Conn_01x06_Pin; PinHeader_1x06_P2.54mm_Vertical
J4, J5, J6, J7: Conn_01x04_Pin; PinHeader_1x04_P2.54mm_Vertical
J11: Conn_01x02_Pin
J13: Conn_02x03_Odd_Even; PinHeader_2x03_P2.54mm_Vertical
R1, R2, R3, R4, R6, R7, R8: 10K; R_0805_2012Metric

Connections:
+3.3V: R1.2, R2.2, R3.2, R4.2, R6.2, R7.2, R8.2; also elsewhere on the board
/Microcontroller/FC1: J1.1, R1.1; also elsewhere on the board
/Microcontroller/FC2: J8.1, R2.1; also elsewhere on the board
/Microcontroller/FC3: J9.1, R3.1; also elsewhere on the board
/Microcontroller/FC4: J10.1, R4.1; also elsewhere on the board
/Microcontroller/M1A: J2.2; also elsewhere on the board
/Microcontroller/M1B: J2.3; also elsewhere on the board
/Microcontroller/M1C: J2.4; also elsewhere on the board
/Microcontroller/M1D: J2.5; also elsewhere on the board
/Microcontroller/M2A: J3.2; also elsewhere on the board
/Microcontroller/M2B: J3.3; also elsewhere on the board
/Microcontroller/M2C: J3.4; also elsewhere on the board
/Microcontroller/M2D: J3.5; also elsewhere on the board
/Microcontroller/PWM_EN_1: J2.1, J2.6; also elsewhere on the board
/Microcontroller/PWM_EN_2: J3.1, J3.6; also elsewhere on the board
/Stepper_Motor_driver1/OUT_1: J5.1; also elsewhere on the board
/Stepper_Motor_driver1/OUT_2: J5.2; also elsewhere on the board
/Stepper_Motor_driver1/OUT_3: J5.3; also elsewhere on the board
/Stepper_Motor_driver1/OUT_4: J5.4; also elsewhere on the board
/Stepper_Motor_driver2/OUT_1: J6.1; also elsewhere on the board
/Stepper_Motor_driver2/OUT_2: J6.2; also elsewhere on the board
/Stepper_Motor_driver2/OUT_3: J6.3; also elsewhere on the board
/Stepper_Motor_driver2/OUT_4: J6.4; also elsewhere on the board
/Stepper_Motor_driver3/OUT_1: J7.1; also elsewhere on the board
/Stepper_Motor_driver3/OUT_2: J7.2; also elsewhere on the board
/Stepper_Motor_driver3/OUT_3: J7.3; also elsewhere on the board
/Stepper_Motor_driver3/OUT_4: J7.4; also elsewhere on the board
/Stepper_Motor_driver/MS1: J13.2, R6.1; also elsewhere on the board
/Stepper_Motor_driver/MS2: J13.4, R7.1; also elsewhere on the board
/Stepper_Motor_driver/MS3: J13.6, R8.1; also elsewhere on the board
/Stepper_Motor_driver/OUT_1: J4.1; also elsewhere on the board
/Stepper_Motor_driver/OUT_2: J4.2; also elsewhere on the board
/Stepper_Motor_driver/OUT_3: J4.3; also elsewhere on the board
/Stepper_Motor_driver/OUT_4: J4.4; also elsewhere on the board
GND: J1.2, J8.2, J9.2, J10.2, J13.1, J13.3, J13.5; also elsewhere on the board

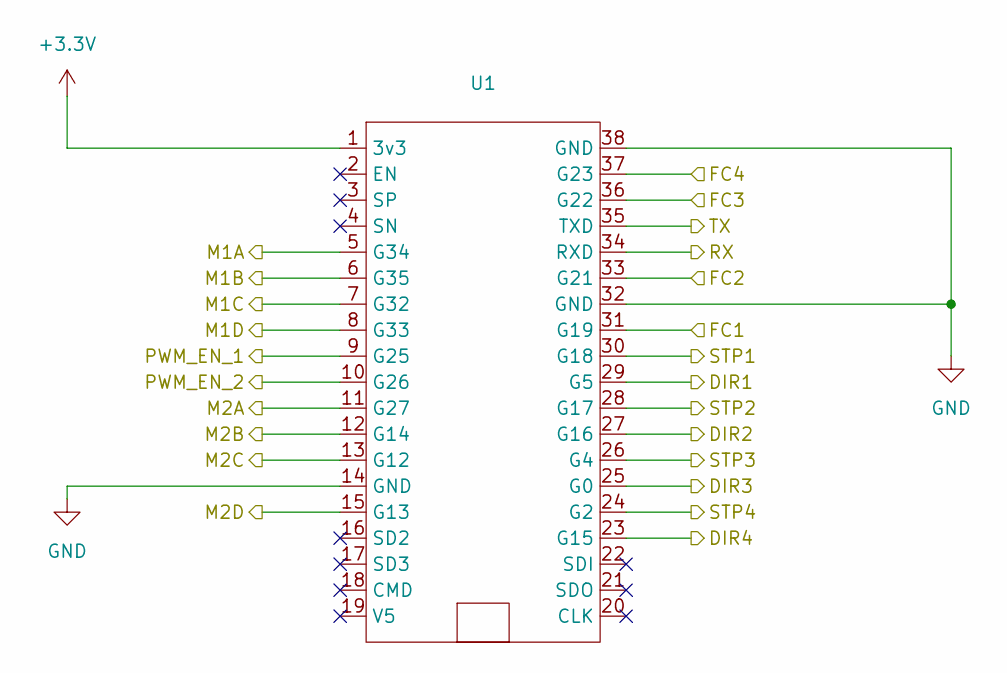
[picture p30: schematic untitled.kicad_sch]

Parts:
U1: DIP-38_1000_ELL

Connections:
+3.3V: U1.1 (3v3); also elsewhere on the board
/Microcontroller/DIR1: U1.29 (G5); also elsewhere on the board
/Microcontroller/DIR2: U1.27 (G16); also elsewhere on the board
/Microcontroller/DIR3: U1.25 (G0); also elsewhere on the board
/Microcontroller/DIR4: U1.23 (G15); also elsewhere on the board
/Microcontroller/FC1: U1.31 (G19); also elsewhere on the board
/Microcontroller/FC2: U1.33 (G21); also elsewhere on the board
/Microcontroller/FC3: U1.36 (G22); also elsewhere on the board
/Microcontroller/FC4: U1.37 (G23); also elsewhere on the board
/Microcontroller/M1A: U1.5 (G34); also elsewhere on the board
/Microcontroller/M1B: U1.6 (G35); also elsewhere on the board
/Microcontroller/M1C: U1.7 (G32); also elsewhere on the board
/Microcontroller/M1D: U1.8 (G33); also elsewhere on the board
/Microcontroller/M2A: U1.11 (G27); also elsewhere on the board
/Microcontroller/M2B: U1.12 (G14); also elsewhere on the board
/Microcontroller/M2C: U1.13 (G12); also elsewhere on the board
/Microcontroller/M2D: U1.15 (G13); also elsewhere on the board
/Microcontroller/PWM_EN_1: U1.9 (G25); also elsewhere on the board
/Microcontroller/PWM_EN_2: U1.10 (G26); also elsewhere on the board
/Microcontroller/RX: U1.34 (RXD)
/Microcontroller/STP1: U1.30 (G18); also elsewhere on the board
/Microcontroller/STP2: U1.28 (G17); also elsewhere on the board
/Microcontroller/STP3: U1.26 (G4); also elsewhere on the board
/Microcontroller/STP4: U1.24 (G2); also elsewhere on the board
/Microcontroller/TX: U1.35 (TXD)
GND: U1.14 (GND), U1.32 (GND), U1.38 (GND); also elsewhere on the board

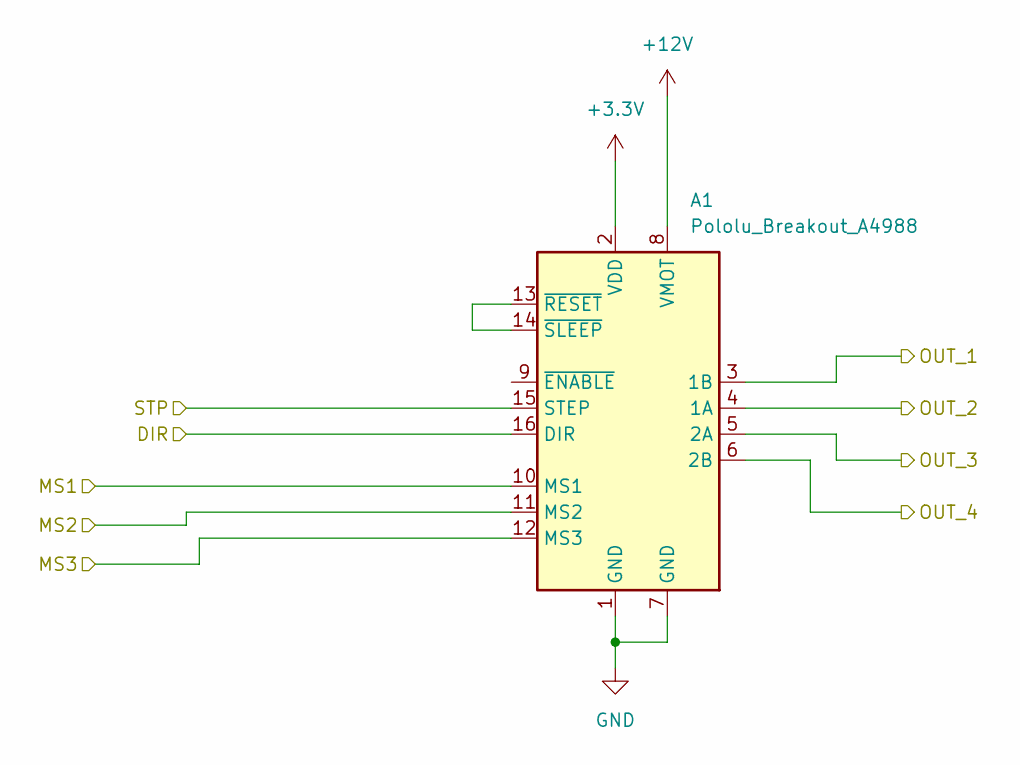
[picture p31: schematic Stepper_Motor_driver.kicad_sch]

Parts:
A1: Pololu_Breakout_A4988; Pololu_Breakout-16_15.2x20.3mm

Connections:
+3.3V: A1.2 (VDD); also elsewhere on the board
+12V: A1.8 (VMOT); also elsewhere on the board
/Microcontroller/DIR1: A1.16 (DIR); also elsewhere on the board
/Microcontroller/STP1: A1.15 (STEP); also elsewhere on the board
/Stepper_Motor_driver/MS1: A1.10 (MS1); also elsewhere on the board
/Stepper_Motor_driver/MS2: A1.11 (MS2); also elsewhere on the board
/Stepper_Motor_driver/MS3: A1.12 (MS3); also elsewhere on the board
/Stepper_Motor_driver/OUT_1: A1.3 (1B); also elsewhere on the board
/Stepper_Motor_driver/OUT_2: A1.4 (1A); also elsewhere on the board
/Stepper_Motor_driver/OUT_3: A1.5 (2A); also elsewhere on the board
/Stepper_Motor_driver/OUT_4: A1.6 (2B); also elsewhere on the board
GND: A1.1 (GND), A1.7 (GND); also elsewhere on the board
unnamed: A1.13 (~RESET), A1.14 (~SLEEP)

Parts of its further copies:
A2, A3, A4: Pololu_Breakout_A4988; Pololu_Breakout-16_15.2x20.3mm

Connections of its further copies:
+3.3V: A2.2 (VDD), A3.2 (VDD), A4.2 (VDD); also elsewhere on the board
+12V: A2.8 (VMOT), A3.8 (VMOT), A4.8 (VMOT); also elsewhere on the board
/Microcontroller/DIR2: A2.16 (DIR); also elsewhere on the board
/Microcontroller/DIR3: A3.16 (DIR); also elsewhere on the board
/Microcontroller/DIR4: A4.16 (DIR); also elsewhere on the board
/Microcontroller/STP2: A2.15 (STEP); also elsewhere on the board
/Microcontroller/STP3: A3.15 (STEP); also elsewhere on the board
/Microcontroller/STP4: A4.15 (STEP); also elsewhere on the board
/Stepper_Motor_driver1/OUT_1: A2.3 (1B); also elsewhere on the board
/Stepper_Motor_driver1/OUT_2: A2.4 (1A); also elsewhere on the board
/Stepper_Motor_driver1/OUT_3: A2.5 (2A); also elsewhere on the board
/Stepper_Motor_driver1/OUT_4: A2.6 (2B); also elsewhere on the board
/Stepper_Motor_driver2/OUT_1: A3.3 (1B); also elsewhere on the board
/Stepper_Motor_driver2/OUT_2: A3.4 (1A); also elsewhere on the board
/Stepper_Motor_driver2/OUT_3: A3.5 (2A); also elsewhere on the board
/Stepper_Motor_driver2/OUT_4: A3.6 (2B); also elsewhere on the board
/Stepper_Motor_driver3/OUT_1: A4.3 (1B); also elsewhere on the board
/Stepper_Motor_driver3/OUT_2: A4.4 (1A); also elsewhere on the board
/Stepper_Motor_driver3/OUT_3: A4.5 (2A); also elsewhere on the board
/Stepper_Motor_driver3/OUT_4: A4.6 (2B); also elsewhere on the board
/Stepper_Motor_driver/MS1: A2.10 (MS1), A3.10 (MS1), A4.10 (MS1); also elsewhere on the board
/Stepper_Motor_driver/MS2: A2.11 (MS2), A3.11 (MS2), A4.11 (MS2); also elsewhere on the board
/Stepper_Motor_driver/MS3: A2.12 (MS3), A3.12 (MS3), A4.12 (MS3); also elsewhere on the board
GND: A2.1 (GND), A2.7 (GND), A3.1 (GND), A3.7 (GND), A4.1 (GND), A4.7 (GND); also elsewhere on the board
unnamed: A2.13 (~RESET), A2.14 (~SLEEP)
unnamed: A3.13 (~RESET), A3.14 (~SLEEP)
unnamed: A4.13 (~RESET), A4.14 (~SLEEP)

Board: 2 copper layers, 23 parts (0 on the bottom side), 48 nets, no tracks yet.

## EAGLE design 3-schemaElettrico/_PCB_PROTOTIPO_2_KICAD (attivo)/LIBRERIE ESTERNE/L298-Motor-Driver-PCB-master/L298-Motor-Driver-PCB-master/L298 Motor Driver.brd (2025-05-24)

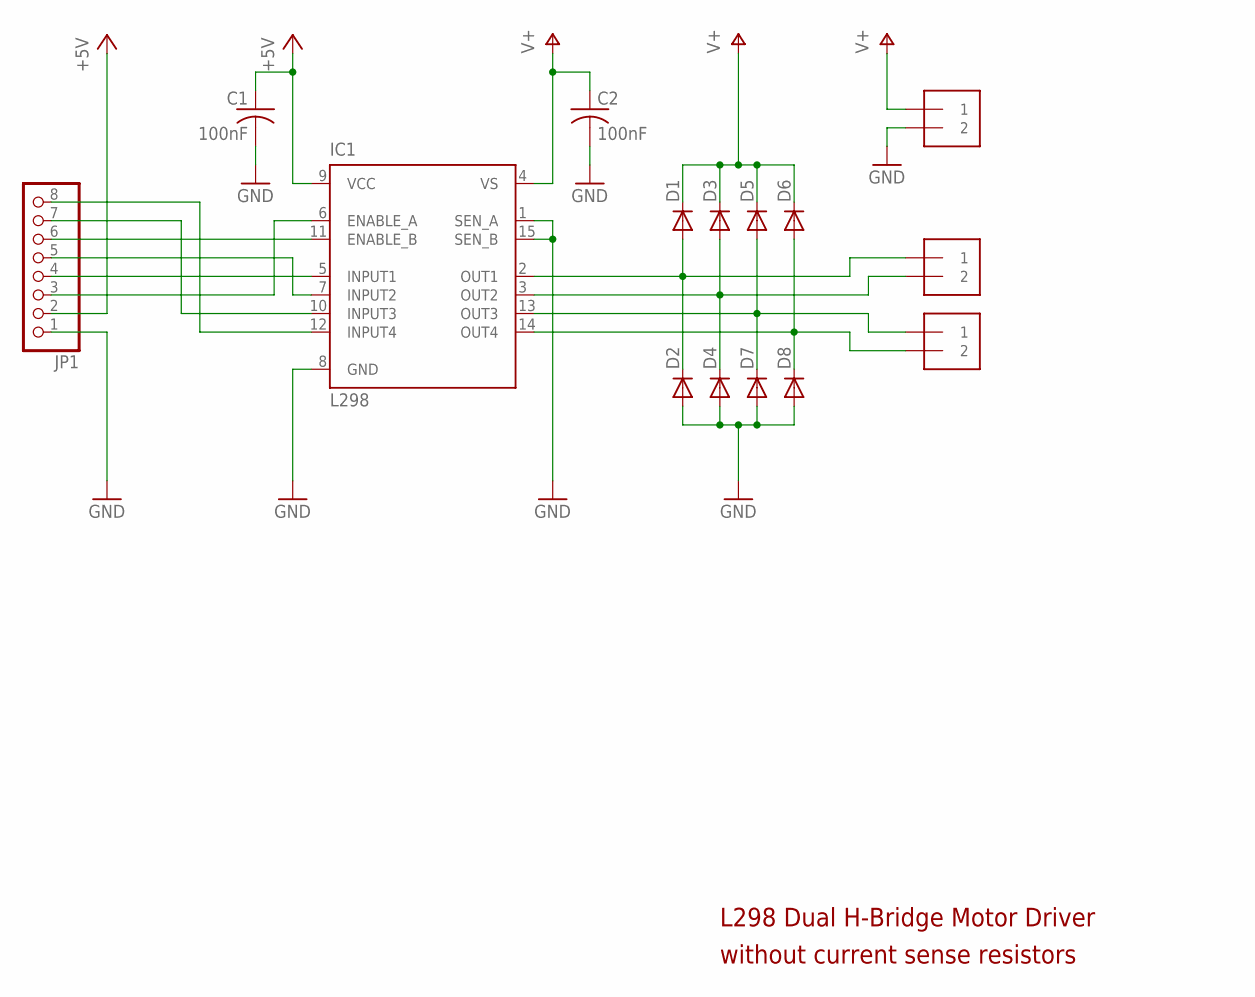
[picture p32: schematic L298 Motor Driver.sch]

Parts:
C1, C2: 100nF; C050-024X044
D1, D2, D3, D4, D5, D6, D7, D8: DIODE-D-5; D-5
IC1: L298; MULTIWATT-15
J1, J2, J3: 1X2-3.5MM
JP1: PINHD-1X8; 1X08

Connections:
+5V: C1.1, IC1.9 (VCC), JP1.2
GND: C1.2, C2.2, D2.A, D4.A, D7.A, D8.A, IC1.1 (SEN_A), IC1.8 (GND), IC1.15 (SEN_B), J1.2, JP1.1
unnamed: D1.A, D2.C, IC1.2 (OUT1), J2.1
unnamed: D3.A, D4.C, IC1.3 (OUT2), J2.2
unnamed: D6.A, D8.C, IC1.14 (OUT4), J3.2
unnamed: D5.A, D7.C, IC1.13 (OUT3), J3.1
unnamed: IC1.5 (INPUT1), JP1.4
unnamed: IC1.7 (INPUT2), JP1.5
unnamed: IC1.6 (ENABLE_A), JP1.3
unnamed: IC1.11 (ENABLE_B), JP1.6
unnamed: IC1.10 (INPUT3), JP1.7
unnamed: IC1.12 (INPUT4), JP1.8
V+: C2.1, D1.C, D3.C, D5.C, D6.C, IC1.4 (VS), J1.1

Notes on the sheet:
L298 Dual H-Bridge Motor Driver
without current sense resistors

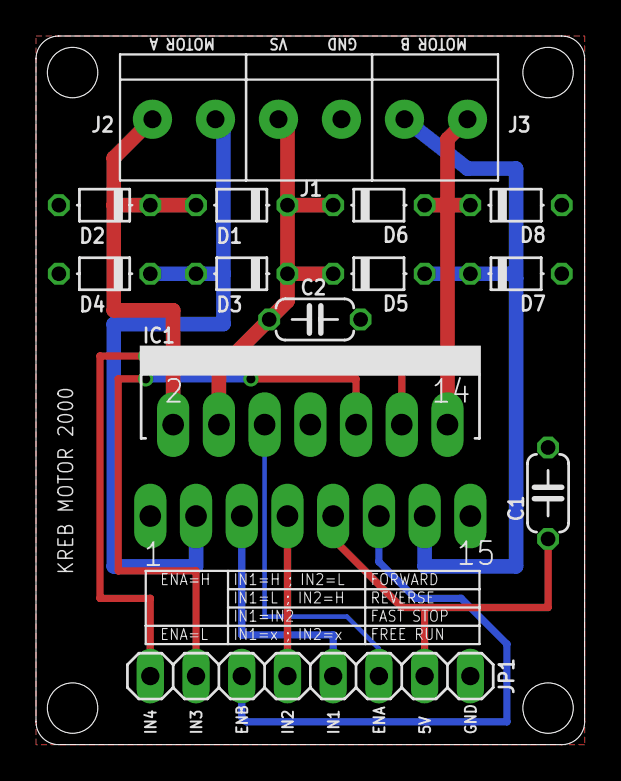
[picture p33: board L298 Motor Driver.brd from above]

Board: 2 copper layers, 30.5 x 39.4 mm, 15 parts (0 on the bottom side), 13 nets.

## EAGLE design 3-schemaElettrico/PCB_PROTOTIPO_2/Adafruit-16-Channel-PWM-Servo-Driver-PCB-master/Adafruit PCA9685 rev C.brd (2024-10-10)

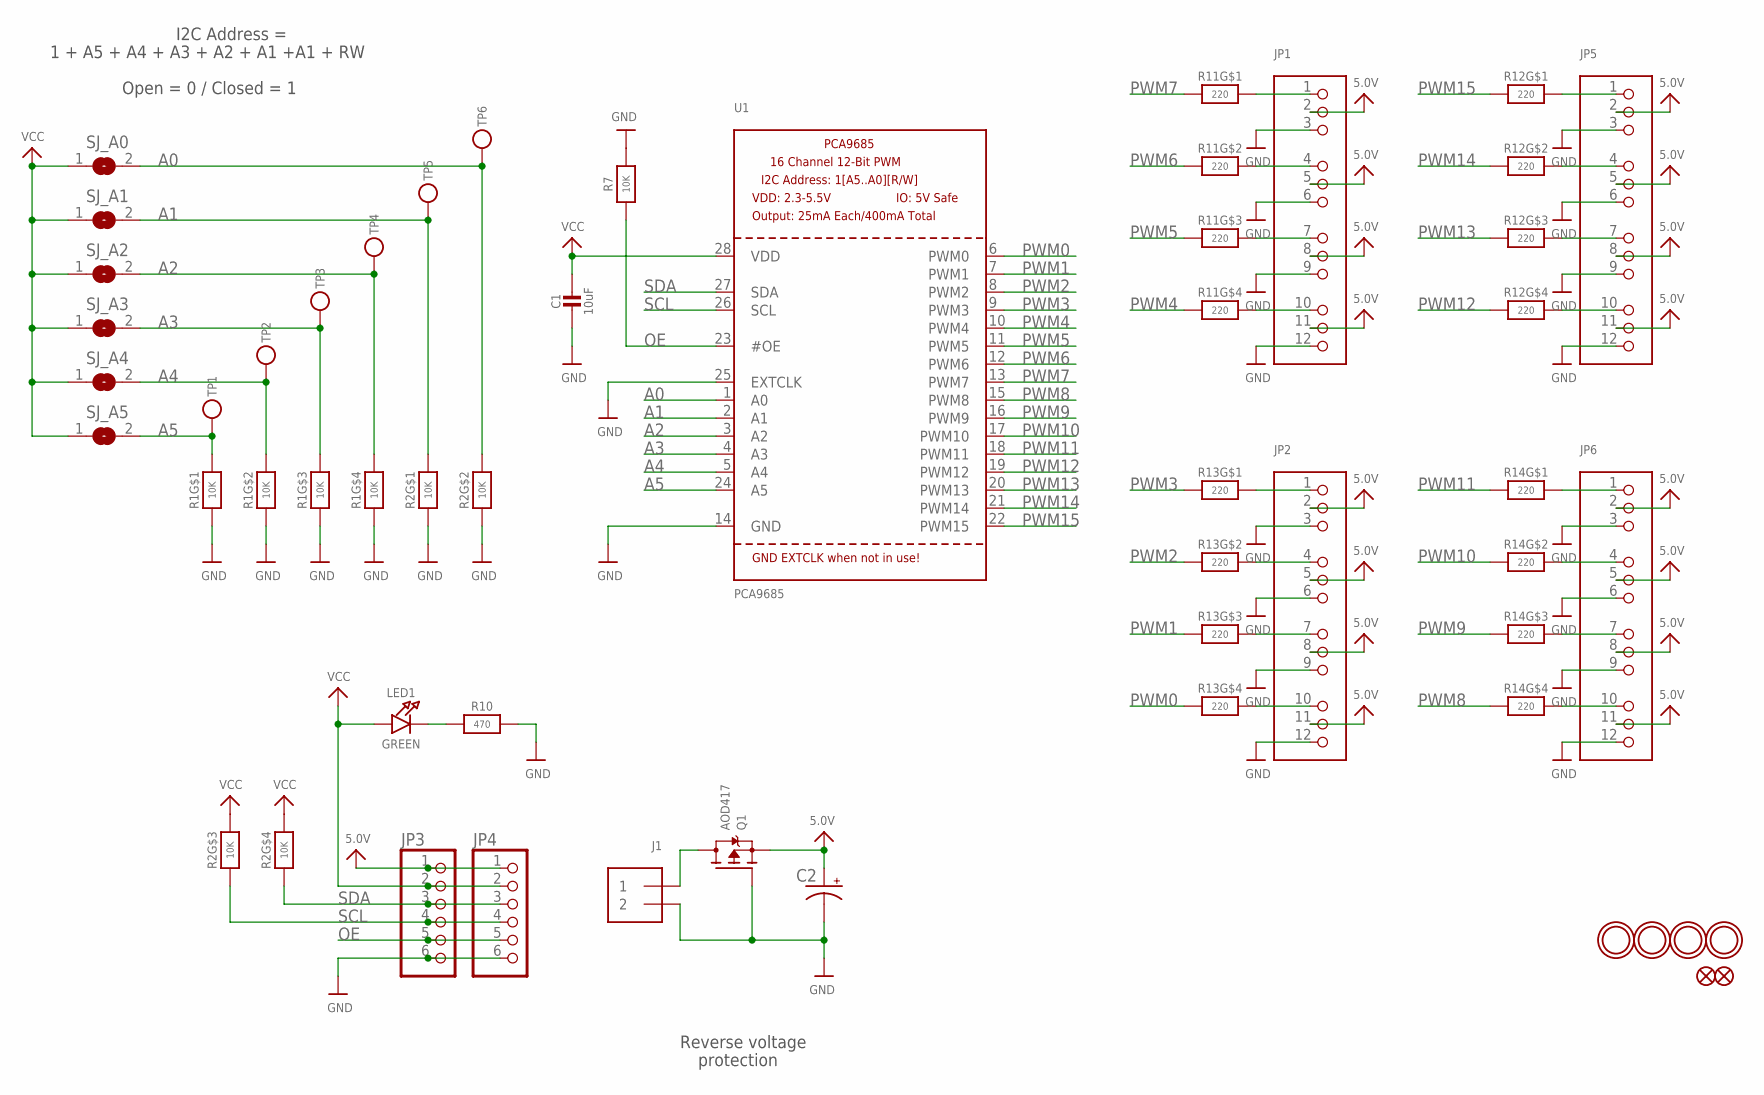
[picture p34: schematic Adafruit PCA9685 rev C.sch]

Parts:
C1: 10uF; 0805-NO
C2: CPOL-USE3.5-8; E3,5-8
FID1, FID2: FIDUCIAL""; FIDUCIAL_1MM
J1: TERMBLOCK_1X2; TERMBLOCK_1X2-3.5MM
JP1, JP2, JP5, JP6: HEADER-3X04; 3X04
JP3, JP4: PINHD-1X6CB; 1X06-CLEANBIG
LED1: GREEN; CHIPLED_0805_NOOUTLINE
Q1: AOD417; TO252
R1, R2: 10K; RESPACK_4X0603
R7: 10K; 0805-NO
R10: 470; _0805MP
R11, R12, R13, R14: 220; RESPACK_4X0603
SJ_A0, SJ_A1, SJ_A2, SJ_A3, SJ_A4, SJ_A5: SOLDERJUMPERREFLOW_NOPASTE; SOLDERJUMPER_REFLOW_NOPASTE
TP1, TP2, TP3, TP4, TP5, TP6: TESTPOINTROUND1MM; TESTPOINT_ROUND_1MM
U1: PCA9685; TSSOP28
U$47, U$48, U$49, U$50: MOUNTINGHOLE2.5; MOUNTINGHOLE_2.5_PLATED

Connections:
5.0V: C2.+, JP1.2, JP1.5, JP1.8, JP1.11, JP2.2, JP2.5, JP2.8, JP2.11, JP3.1, JP4.1, JP5.2, JP5.5, JP5.8, JP5.11, JP6.2, JP6.5, JP6.8, JP6.11, Q1.2 (S)
A0: R2.7 (2), SJ_A0.2, TP6.P$1, U1.1 (A0)
A1: R2.8 (2), SJ_A1.2, TP5.P$1, U1.2 (A1)
A2: R1.5 (2), SJ_A2.2, TP4.P$1, U1.3 (A2)
A3: R1.6 (2), SJ_A3.2, TP3.P$1, U1.4 (A3)
A4: R1.7 (2), SJ_A4.2, TP2.P$1, U1.5 (A4)
A5: R1.8 (2), SJ_A5.2, TP1.P$1, U1.24 (A5)
GND: C1.2, C2.-, J1.2, JP1.3, JP1.6, JP1.9, JP1.12, JP2.3, JP2.6, JP2.9, JP2.12, JP3.6, JP4.6, JP5.3, JP5.6, JP5.9, JP5.12, JP6.3, JP6.6, JP6.9, JP6.12, Q1.1 (G), R1.1, R1.2 (1), R1.3 (1), R1.4 (1), R2.1, R2.2 (1), R7.2, R10.2, U1.14 (GND), U1.25 (EXTCLK)
unnamed: LED1.C, R10.1
unnamed: JP1.4, R11.7 (2)
unnamed: JP1.1, R11.8 (2)
unnamed: JP1.7, R11.6 (2)
unnamed: JP1.10, R11.5 (2)
unnamed: JP2.1, R13.8 (2)
unnamed: JP2.4, R13.7 (2)
unnamed: JP2.7, R13.6 (2)
unnamed: JP2.10, R13.5 (2)
unnamed: JP6.10, R14.5 (2)
unnamed: JP6.7, R14.6 (2)
unnamed: JP6.4, R14.7 (2)
unnamed: JP6.1, R14.8 (2)
unnamed: JP5.10, R12.5 (2)
unnamed: JP5.7, R12.6 (2)
unnamed: JP5.4, R12.7 (2)
unnamed: JP5.1, R12.8 (2)
OE: JP3.5, JP4.5, R7.1, U1.23 (#OE)
PWM0: R13.4 (1), U1.6 (PWM0)
PWM1: R13.3 (1), U1.7 (PWM1)
PWM2: R13.2 (1), U1.8 (PWM2)
PWM3: R13.1, U1.9 (PWM3)
PWM4: R11.4 (1), U1.10 (PWM4)
PWM5: R11.3 (1), U1.11 (PWM5)
PWM6: R11.2 (1), U1.12 (PWM6)
PWM7: R11.1, U1.13 (PWM7)
PWM8: R14.4 (1), U1.15 (PWM8)
PWM9: R14.3 (1), U1.16 (PWM9)
PWM10: R14.2 (1), U1.17 (PWM10)
PWM11: R14.1, U1.18 (PWM11)
PWM12: R12.4 (1), U1.19 (PWM12)
PWM13: R12.3 (1), U1.20 (PWM13)
PWM14: R12.2 (1), U1.21 (PWM14)
PWM15: R12.1, U1.22 (PWM15)
PWRIN: J1.1, Q1.3 (D)
SCL: JP3.4, JP4.4, R2.3 (1), U1.26 (SCL)
SDA: JP3.3, JP4.3, R2.4 (1), U1.27 (SDA)
VCC: C1.1, JP3.2, JP4.2, LED1.A, R2.5 (2), R2.6 (2), SJ_A0.1, SJ_A1.1, SJ_A2.1, SJ_A3.1, SJ_A4.1, SJ_A5.1, U1.28 (VDD)

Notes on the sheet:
Reverse voltage
protection
1 + A5 + A4 + A3 + A2 + A1 +A1 + RW
I2C Address =
Open = 0 / Closed = 1

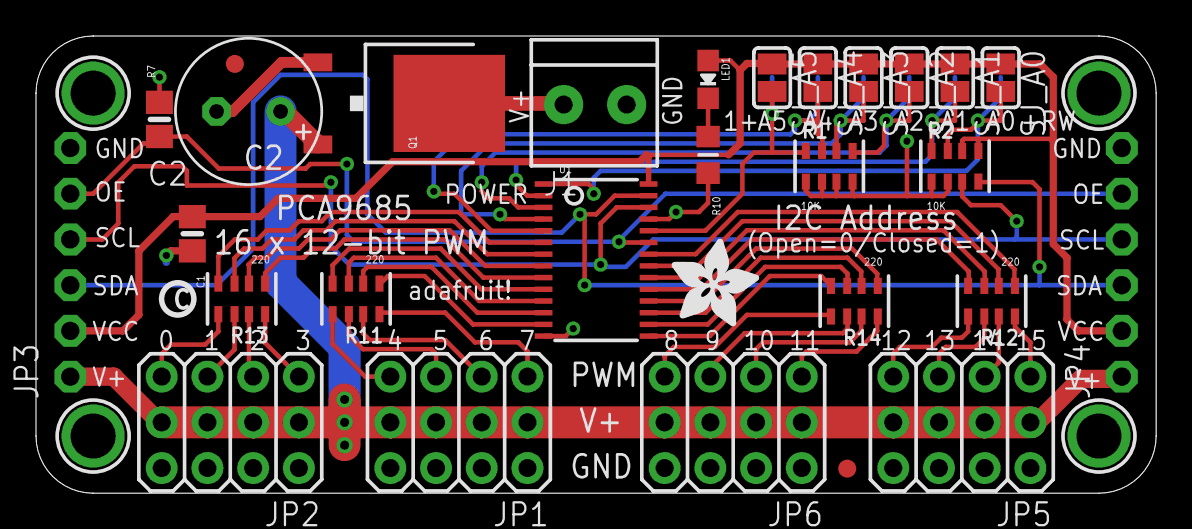
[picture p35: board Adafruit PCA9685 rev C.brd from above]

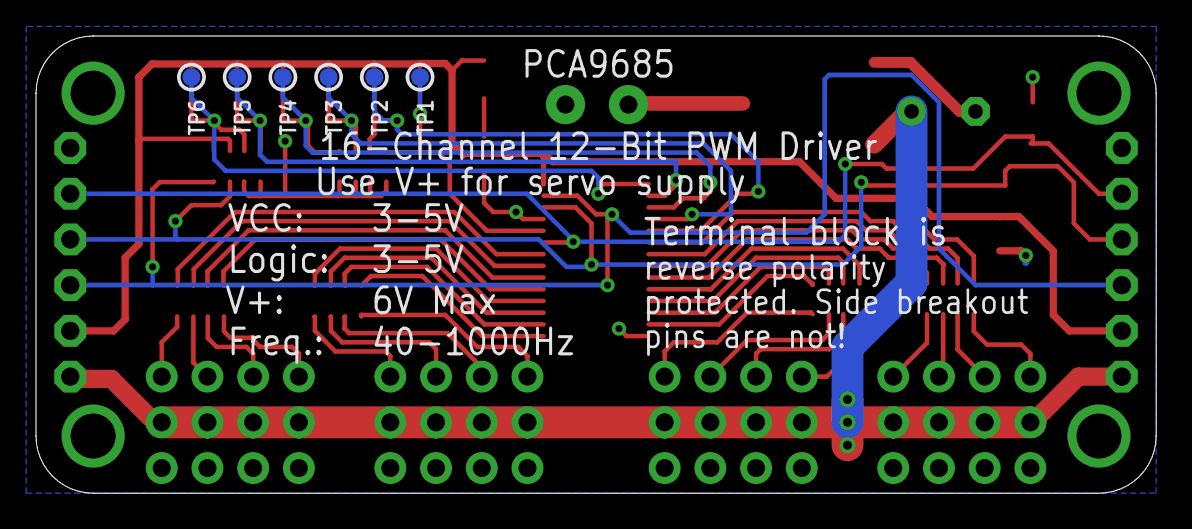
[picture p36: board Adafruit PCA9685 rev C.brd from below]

Board: 2 copper layers, 62.2 x 25.4 mm, 40 parts (6 on the bottom side), 46 nets.

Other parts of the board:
U$51: ADAFRUIT_5MM
U$54: PCBFEAT-REV-040

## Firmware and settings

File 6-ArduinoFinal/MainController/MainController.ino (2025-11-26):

#include "Serial_communication.h"
//#include "PIN_OUT_FINAL.h"
//#include "Stepper2.h"
//#include "Sonar_Completo_Leonardo.h"
//#include "SoftwareSerial.h"
//#include "Movement.h"
#include <ESP32Servo.h>
#include <math.h>
#include "Sonar_v2.h"


/*
Stepper Stepper1(stepsPerRevolution, dir_step1,step1);
Stepper Stepper2(stepsPerRevolution, dir_step2,step2);
Stepper Stepper3(stepsPerRevolution, dir_step3,step3);
Stepper Stepper4(stepsPerRevolution, dir_step4,step4);  */


String stringa = "aaaaa";
String stringaold = "";
String stringaoldold = "";
String mex = "H";
char state='H';
uint8_t speed=255;
String mex_read = "aaa";

uint8_t mex_to_proc = 0;    //pointer of the message to be processed
uint8_t mex_last = 0;       //pointer of the last message received
const int bit_dim_buffer = 4; //2^bit_dim_buffer sets dimension of the buffer, and pointer%2^bit_dim_buffer gives the position inside the buffer of the mex selected
const int dim_array = 2^bit_dim_buffer;
String array_mex[dim_array];
bool new_mex = false; 
//int lenght = 10;
//char mess[lenght] = "";
unsigned long timeout=5000;
unsigned long lastmillis=0;

int time_0 = 0;
int time_1 = 0;
int delta = 0;

int pwm_new = 0;

//const int minAngle = 15;
//const int maxAngle = 165;
int sonar_index = minAngle;
bool direction = true; //true 15 -> 165       false 165 -> 15

bool movementAuthorized = true;  //variable to lock dc movement locally from signal too close to sonar sensor
//true: controlled by serial communication
//false: controlled by manual controller

void setup() {

  pinMode(dir_dc1_2, OUTPUT);
  pinMode(dir_dc2_2, OUTPUT);
  pinMode(dir_dc3_2, OUTPUT);
  pinMode(dir_dc4_2, OUTPUT);

  pinMode(dir_dc1, OUTPUT);
  pinMode(dir_dc2, OUTPUT);
  pinMode(dir_dc3, OUTPUT);
  pinMode(dir_dc4, OUTPUT);
  pinMode(PWM_PIN, OUTPUT);

  pinMode(dir_step1, OUTPUT);
  pinMode(dir_step2, OUTPUT);
  pinMode(dir_step3, OUTPUT);
  pinMode(dir_step4, OUTPUT);

  pinMode(step1, OUTPUT);
  pinMode(step2, OUTPUT);
  pinMode(step3, OUTPUT);
  pinMode(step4, OUTPUT);
  pinMode(controller, INPUT);

  pinMode(trigPin, OUTPUT);
  pinMode(echoPin, INPUT);
  myservo.attach(33);
  
  //security measure
  analogWrite(PWM_PIN, 0);

  //serialCommCloser();
  delay(1000);
  serialCommOpener();
  serialWriter("Leonardo ready");
}

/*
    ###   DC DIRECTION    ###

F   ->  Leonardo moving forward
B   ->  Leonardo moving backwards
L   ->  Leonardo turning  left
R   ->  Leonardo turning right

    ###   STEPPER DIRECTION   ###

S1U  ->  moving front axis up
S1D  ->  moving front axis down
S2U  ->  moving middle axis up
S2D  ->  moving middle axis down
S3U  ->  moving back axis up
S3D  ->  moving back axis down
S4U  ->  moving balance axis up
S4D  ->  moving balance axis down

PKKK  -> setting pwm to values between 0 and 255, managed in KKK

O     ->  pwm default value 0 
I     ->  pwm default value 255
*/

void test_esp(){

  /*delay(500);
  digitalWrite(dir_dc_1,HIGH);
  delay(500);
  digitalWrite(dir_dc_1,LOW);
*/
}


void loop() {

  //if (millis() - lastmillis > timeout) state = 'H';
  //Serial.println("aaa");
  
  if (Serial.available()) {
    String mex = Serial.readStringUntil('\n');
    char chr = mex.charAt(0);

    Serial.println(chr);
    Serial.print("recived:");
    Serial.println(mex);

    //Serial.println("000000");
    //serialWriter(mex+" entrato in gestione dc");
    
    
    if(chr == 'Y'){

        serialCommCloser();
    }
    
    else  if(chr == 'P'){
        pwm_new = 0;
        if(mex[1]>'0' && mex[1]<='9'){
          pwm_new += (int(mex[1])-48)*100;  
        }
        else if(mex[2]>'0' && mex[2]<='9'){
          pwm_new += (int(mex[2])-48)*10;  
        }
        else if(mex[3]>'0' && mex[3]<='9'){
          pwm_new += (int(mex[3])-48);  
        }
        //pwm_new = (int(mex[1])-48)*100 + (int(mex[2])-48)*10 + (int(mex[3])-48);
        set_pwm(pwm_new);
        String stringa = "new pwm setted at "+String(pwm_new)+" ";
        serialWriter(stringa);
    }

    else  if(chr == 'O'){
      
        serialWriter("not moving");
        stop_movement();
        if(time_0){
          
          time_1 = millis();
          delta = (time_1-time_0);
          String stringa = "moved for "+String(delta)+" milliseconds";
          serialWriter(stringa);
          time_0 = time_1 = 0;
        }
    }
    else  if(chr == 'I'){
        default_movement();
        time_0 = millis();
        serialWriter("moving");
    }
    
    else  if(chr == 'S'){
      
        bool_dir = false;

        if(mex.charAt(2) == 'U'){
          bool_dir = true;
        }
      
        switch(mex.charAt(1)){
          case 1:

              //moveAxis gets as input parameters (int dir_pin_axis, int step_pin_axis, bool direction, int timer_microseconds)
            moveAxis(dir_dc1, step1, bool_dir, timer_micro);
            delay(500);

            break;

          case 2:

            //moveAxis gets as input parameters (int dir_pin_axis, int step_pin_axis, bool direction, int timer_microseconds)
            moveAxis(dir_dc2, step2, bool_dir, timer_micro);
            delay(500);  
    
            break;

          case 3:

            //moveAxis gets as input parameters (int dir_pin_axis, int step_pin_axis, bool direction, int timer_microseconds)
            moveAxis(dir_dc3, step3, bool_dir, timer_micro);
            delay(500);  

            break;

          case 4:

            //moveAxis gets as input parameters (int dir_pin_axis, int step_pin_axis, bool direction, int timer_microseconds)
            moveAxis(dir_dc4, step4, bool_dir, timer_micro);
            delay(500); 

            break;

          default:

            //serialWriter("Something's wrong, i can feel it");
            stop_movement();
    
            break;
       }
    }
      
    

    else{
      if(movementAuthorized){

        switch(chr){
          case 'F':
            //Serial.println("0000FFF0");
            stop_movement();
            delay(100);
            serialWriter("avanti");
            forward_mov();
            default_movement();
            

            break;

          case 'B':
            stop_movement();
            delay(100);
            back_mov();
            serialWriter("indietro");
            default_movement();

            break;

          case 'L':
            stop_movement();
            delay(100);
            left_mov();
            serialWriter("sinistra");
            default_movement();
            break;

          case 'R':
            stop_movement();
            delay(100);
            right_mov();
            serialWriter("destra");
            default_movement();
            break;       

          default:
          //default block everything
            stop_movement();
            serialWriter("Something's wrong, i can feel it");
            delay(100);
            serialWriter(mex);

            break;
        } 
        //printing phase and module for the sonar sscanner
        //serialWriter(String(sonar_index)+";"+String(scan_point(sonar_index)));
      //scan_point(sonar_index);
        
      }
      //printing phase and module for the sonar sscanner
      
  
      else if(movementAuthorized == false){
          int temp = analogRead(controller);
          serialWriter(String(temp));

          if (temp<2600 && temp>=2500){
                  stop_movement();
                  delay(100);
                  serialWriter("avanti");
                  forward_mov();
                  default_movement();
          }
          else if (temp<1750 && temp>=1600){
                  stop_movement();
                  delay(100);
                  back_mov();
                  serialWriter("indietro");
                  default_movement();
          }
          else if (temp<1000 && temp>=800){
                  stop_movement();
                  delay(100);
                  left_mov();
                  serialWriter("sinistra");
                  default_movement();
          }
          else if (temp<2200 && temp>2000){
                  stop_movement();
                  delay(100);
                  right_mov();
                  serialWriter("destra");
                  default_movement();
          }

          else if(temp<=50){
              stop_movement();
              delay(100);
              serialWriter("Leonardo Fermo");   
          }
          

      }
    }

    
 
  }
  
  if(direction){
      sonar_index++;
      if(sonar_index == maxAngle){
          direction = false;
      }
    }
    else{
      sonar_index--;
      if(sonar_index == minAngle){
        direction = true;
      }
    }
    
    serialWriter("D:"+String(sonar_index)+";"+String(scan_point(sonar_index)));
}

/*
void toBeTested(){

  if (Serial.available()) {
    mex_read = Serial.readString();
    Serial.print("recived:");
    Serial.println(mex_read);
    new_mex = true;
    String aux_mex = "aaa";
    if(mex_read.length()<2^bit_dim_buffer){
      for(int i = 0; i<mex_read.length(); i++){
        array_mex[(i+mex_last)%2^bit_dim_buffer] = mex_read.charAt(i); 
      }
      mex_last = mex_last + mex_read.length();
    }
    else {
      serialWriter("error: buffer overflow");
      new_mex=false; 
    }
    
    while(mex_last != mex_to_proc){
      if(!(mex_last%2^bit_dim_buffer == mex_to_proc%2^bit_dim_buffer)){
        if(mex.charAt(0) == 'P'){
          set_pwm(int(mex[1])*100 + int(mex[2])*10 + int(mex[3]));
        }

        else if(mex.charAt(0) == 'O'){
          serialWriter("not moving");
          stop_movement();
        }
        else if(mex.charAt(0) == 'I'){
          default_movement();
          serialWriter("moving");
        }

        else if(mex.charAt(0) == 'S'){
          
          bool_dir = false;

          if(mex.charAt(2) == 'U'){
            bool_dir = true;
          }
          
          switch(mex.charAt(1)){
            case 1:

                //moveAxis gets as input parameters (int dir_pin_axis, int step_pin_axis, bool direction, int timer_microseconds)
                moveAxis(dir_dc1, step1, bool_dir, timer_micro);
                delay(500);

            break;

            case 2:

                //moveAxis gets as input parameters (int dir_pin_axis, int step_pin_axis, bool direction, int timer_microseconds)
                  moveAxis(dir_dc2, step2, bool_dir, timer_micro);
                  delay(500);  
        
            break;

            case 3:

                //moveAxis gets as input parameters (int dir_pin_axis, int step_pin_axis, bool direction, int timer_microseconds)
                moveAxis(dir_dc3, step3, bool_dir, timer_micro);
                delay(500);  

            break;

            case 4:

                //moveAxis gets as input parameters (int dir_pin_axis, int step_pin_axis, bool direction, int timer_microseconds)
                  moveAxis(dir_dc4, step4, bool_dir, timer_micro);
                  delay(500); 

            break;

            default:

              serialWriter("Something's wrong, i can feel it");
              stop_movement();
        
            break;
          }
        }
        else{
          serialWriter(mex+" entrato in gestione dc");
          switch(mex.charAt(0)){
            case 'F':

                
                serialWriter("avanti");
              forward_mov();

            break;

            case 'B':

                back_mov();
                serialWriter("indietro");

            break;

            case 'L':

                left_mov();
                serialWriter("sinistra");

            break;

            case 'R':

                right_mov();
                serialWriter("destra");

            break;

            default:
            //default block everything
              serialWriter("Something's wrong, i can feel it");
              serialWriter(mex);
              stop_movement();

              
        
            break;
          }
        }

      }//TODO: FINIRE
      mex_to_proc++;
    }
  }

  

  
  

*/
void serialWriteTest() {

  serialCommOpener();
  for (int i = 0; i < 10; i++) {
    serialWriter("ciao");
    delay(100);
  }
  serialCommCloser();
}

void serialReadTest(String stringa) {
  Serial.println(stringa + " entrato in serialReadTest");
  if (stringa == "12345678") {

    serialCommCloser();
  }
  serialAnalyzer(stringa);
  delay(1000);
}



void dummymovement2() {
  int delay_time = 300;
  forward_mov();


  //default_movement();
  set_pwm(200);
  delay(delay_time);
  //stop_movement();
  set_pwm(0);
  delay(delay_time);

  delay(1000);
  back_mov();

  //default_movement();
  set_pwm(200);
  delay(delay_time);
  //stop_movement();
  set_pwm(0);
  delay(delay_time);

  delay(1000);

  left_mov();

  //default_movement();
  delay(delay_time);
  stop_movement();
  delay(delay_time);

  right_mov();

  //default_movement();
  delay(delay_time);
  stop_movement();
  delay(delay_time);
}

void dummyStepper() {

  moveAxis(dir_dc1, step1, true, timer_micro);
  delay(500);

  moveAxis(dir_dc1, step1, false, timer_micro);
  delay(500);

  moveAxis(dir_dc2, step2, true, timer_micro);
  delay(500);

  moveAxis(dir_dc2, step2, false, timer_micro);
  delay(500);

  moveAxis(dir_dc3, step3, true, timer_micro);
  delay(500);

  moveAxis(dir_dc3, step3, false, timer_micro);
  delay(500);

  moveAxis(dir_dc4, step4, true, timer_micro);
  delay(500);

  moveAxis(dir_dc4, step4, false, timer_micro);
  delay(500);
}

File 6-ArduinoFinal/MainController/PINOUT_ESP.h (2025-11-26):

#define dir_dc1 16
#define dir_dc2 17
#define dir_dc3 5
#define dir_dc4 18

/// ATTENZIONEE: I PIN DA 6 a 11 non possono essere usati perchè li usa internamente l'esp per scrivere la flash


#define dir_dc1_2 4
#define dir_dc2_2 0
#define dir_dc3_2 2
#define dir_dc4_2 15

#define PWM_PIN 19 

#define dir_step1 24
#define dir_step2 20  
#define dir_step3 21
#define dir_step4 25

#define step1 22
#define step2 23
#define step3 12
#define step4 13

#define controller 14

#define trigPin 26
#define echoPin 27

#define stepsPerRevolution 200 

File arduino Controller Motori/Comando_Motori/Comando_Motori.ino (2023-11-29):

//#include "PIN_OUT.h"
//#include "Set_Orientation.h"
//Stepper Thomas
#include "Stepper_Define.h"
//#include "Stepper_Function.h"
#include "PIN_OUT2.h"
#include "Set_orientation2.h"

#include "Endrun_Functions.h"
#include "Manual_Mode.h"



//Serial Mirko
#include "Serial_Controller.h"


#define DELAY 100
#define MIN 0 // min value of speed
#define MAX 1 // max value of speed


void setup() {

  Serial.begin(9600); // BEGINNING COMUNICATION RATE: 9600 bit/s
  /*
  /*
   * ALL OF THIS PINS ARE DIGITAL
   
  // FOR SERIAL COMUNICATION
   pinMode(TX,INPUT);
   pinMode(RX,OUTPUT);
   
  // H BRIDGE PIN 
   pinMode(STANDBY_R,OUTPUT);
   pinMode(STANDBY_L,OUTPUT);
   
  // ALL THE PINS TO MOVE THE ENGINS ARE IN OUTPUT MODE

  // SET OF PINS FOR PWM TO SET SPEED FROM
   pinMode(PWM_F_R,OUTPUT);
   pinMode(PWM_F_L,OUTPUT);
   pinMode(PWM_B_R,OUTPUT);
   pinMode(PWM_B_L,OUTPUT);
  
  //THIS IS A SET TO INDICATE AND ENABLE THE ENGINES DIRECTION OF ROTATION
   pinMode(CLKW_F_R,OUTPUT);
   pinMode(ACLKW_F_R,OUTPUT);
   pinMode(CLKW_F_L,OUTPUT);
   pinMode(ACLKW_F_L,OUTPUT);
   pinMode(CLKW_B_R,OUTPUT);
   pinMode(ACLKW_B_R,OUTPUT);
   pinMode(CLKW_B_L,OUTPUT);
   pinMode(ACLKW_B_L,OUTPUT);
  
  //pin step motors

  


  
  pinMode(STEP_PIN_F, OUTPUT);
  pinMode(DIR_PIN_F, OUTPUT);

  pinMode(STEP_PIN_C, OUTPUT);
  pinMode(DIR_PIN_C, OUTPUT);

  pinMode(STEP_PIN_B, OUTPUT);
  pinMode(DIR_PIN_B, OUTPUT);

  pinMode(STEP_PIN_CG, OUTPUT);
  pinMode(DIR_PIN_CG, OUTPUT);
  
  
   
   * ALL OF THIS PINS ARE ANALOG
   */
  
  pinMode(pwm, OUTPUT);
  pinMode(dir1, OUTPUT);
  pinMode(dir2, OUTPUT);
  pinMode(dir3, OUTPUT);
  pinMode(dir4, OUTPUT);
  
   
}


void loop() {

  pwm_function(0.5);
  dummyMovement();
  //communicationSerial();

}

void dummyMovement(){
  
  forward_mode();
  delay(1000);
  
  turn_off_orientation_mode();
  delay(100);
  
  backward_mode();
  delay(1000);
  
  turn_off_orientation_mode();
  delay(100);

  turn_left_mode();
  delay(1000);
  
  turn_off_orientation_mode();
  delay(100);

  turn_right_mode();
  delay(1000);
  
  turn_off_orientation_mode();
  delay(100);
  
}

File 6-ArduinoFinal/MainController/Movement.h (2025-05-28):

//#include "Arduino.h"
//#include "PIN_OUT_FINAL.h"

/*
void move(int motor, String direction){
  digitalWrite(motor, direction);
}
*/
//automatic setter of the pwm value in decreasing and increasing pwm value modes
void set_pwm(int pwm_v){
  int pwm_value = analogRead(PWM_PIN);
  if(pwm_v > pwm_value){
    for(int i=pwm_value; i<=pwm_v; i++){
      
      analogWrite(PWM_PIN, i);

    }
    

  }
  else{
    for(int i=pwm_value; i>=pwm_v; i--){
      
      analogWrite(PWM_PIN, i);
    }
    
  }
  
}




//method to stop the movement of the DC mothors
void stop_movement(){
  analogWrite(PWM_PIN, 0);
}

//default value of the PWM signal controlling the DC motors
void default_movement(){
  analogWrite(PWM_PIN, 255);
}


void left_mov(){
  
  
  digitalWrite(dir_dc1, LOW); 
  digitalWrite(dir_dc2, LOW);
  digitalWrite(dir_dc3, HIGH);
  digitalWrite(dir_dc4, HIGH);
  
}

void right_mov(){
  
  digitalWrite(dir_dc1, HIGH);
  digitalWrite(dir_dc2, HIGH);
  digitalWrite(dir_dc3, LOW);
  digitalWrite(dir_dc4, LOW);
  
}

void forward_mov(){
  
  digitalWrite(dir_dc1, LOW);
  digitalWrite(dir_dc2, LOW);
  digitalWrite(dir_dc3, LOW);
  digitalWrite(dir_dc4, LOW);
  
}

void back_mov(){
  
  digitalWrite(dir_dc1, HIGH);
  digitalWrite(dir_dc2, HIGH);
  digitalWrite(dir_dc3, HIGH);
  digitalWrite(dir_dc4, HIGH);
  
}


/*
void moveAxis(Stepper stepper_motor, int how_much_to_rotate) 
{
    // una rotazione in una direzione
    Serial.println("Rotazione in corso");
    stepper_motor.step(how_much_to_rotate);
    delay(1000);

    
}*/

/*
Example sketch to control a stepper motor with A4988 stepper motor driver and Arduino without a library. More info: https://www.makerguides.com 

// Define stepper motor connections and steps per revolution:
#define dirPin1 7
#define stepPin1 8

#define dirPin2 9
#define stepPin2 10

#define dirPin3 11
#define stepPin3 12

#define dirPin4 A0
#define stepPin4 13

#define stepsPerRevolution 200

void setup() {
  // Declare pins as output
}
*/

/*
function for automatic detection of direction and movement of the stepper motor on the linear asix
- dir_pin_axis : abilitation of the motor direction
- step_pin_axis : define direction of the
- direction : define direction of the movement. True = up, False = down
- timer_microseconds : parameter that defines the lenght of the movement

*/

void moveAxis(int dir_pin_axis, int step_pin_axis, bool direction, int timer_microseconds) {

  digitalWrite(dir_pin_axis , HIGH);

  for (int i = 0; i < 5 * stepsPerRevolution; i++) {
  
      digitalWrite(step_pin_axis, direction);
      delayMicroseconds(timer_microseconds);
      digitalWrite(step_pin_axis, !direction);
    
  }
  
  digitalWrite(dir_pin_axis, LOW);
}  
  

float timeMovement (char* c){

  float time_0 = 0;
  float time_0 = 0;
  stop_movement();

  switch (c) {
    case 'F':
      forward_mov();
      
      //analogWrite(PWM_PIN, speed);
      break;
    case 'R':
      right_mov();
      //analogWrite(PWM_PIN, speed);
      break;
    case 'L':
      left_mov();
      //analogWrite(PWM_PIN, speed);
      break;
    case 'B':
      back_mov();
      //analogWrite(PWM_PIN, speed);
      break;

    default:
      println("selected incorrect movement");

    break; 
  }

  

  time_0 = millis();

  default_movement();

  while(c != 'S'){}

  stop_movement();

  time_1 = millis();

  return time_1-time_0;

}

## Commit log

2023-09-27 Upload Onedrive Folder
    [A4988-1.STEP, COSTI E POTENZA DISSIPATA.xlsx, ORIGINE.stl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]
2023-11-29 Fixed - testing needed
    [Comando_Motori.ino, PIN_OUT2.h]
2024-12-11 serial implementing start, stop, pwm change and security lock
2025-03-27 done 74hc238
    [DC_Motor_driver.kicad_sch, Leonardo_v2.0.kicad_pcb, Leonardo_v2.0.kicad_sch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]
2025-04-01 placed nodeMCU
    [Adafruit PCA9685 rev C.brd, Adafruit PCA9685 rev C.sch, Adafruit PCA9685.brd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]
2025-05-11 serial communication opened with esp32, but only works esp->pc
2025-11-26 bug fixing and code lightening
    [MainController.ino, PINOUT_ESP.h, Sonar_v2.h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]
2025-11-26 sonar working finally
2025-11-26 python from raspberry
